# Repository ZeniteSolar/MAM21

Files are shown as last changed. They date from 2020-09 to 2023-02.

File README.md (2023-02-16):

# MAM21
**M**ódulo de **A**cionamento do **M**otor 2021

Embarcação Guarapuvu II

Equipe Zênite Solar

### About
High current >150A Electronic Speed Controller for **[ME0909](https://www.electricmotorsport.com/me0909-pmdc-motor-12-48v-4-hp-cont-12-8-hp-pk.html)** motor, with CANBus.

### Images

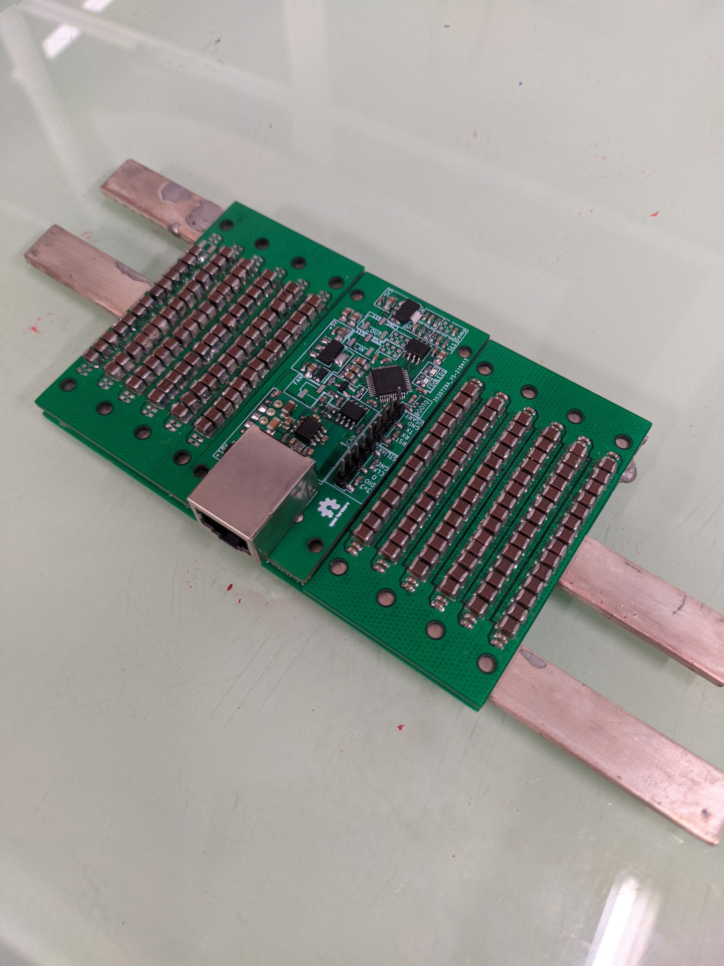
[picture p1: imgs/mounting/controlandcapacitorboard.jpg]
board

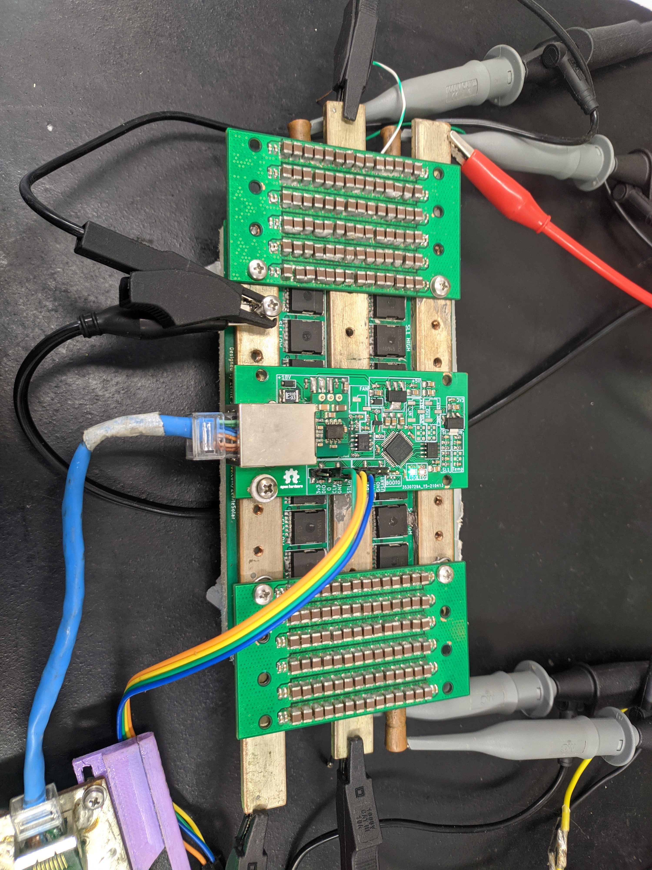
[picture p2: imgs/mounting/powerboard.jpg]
board

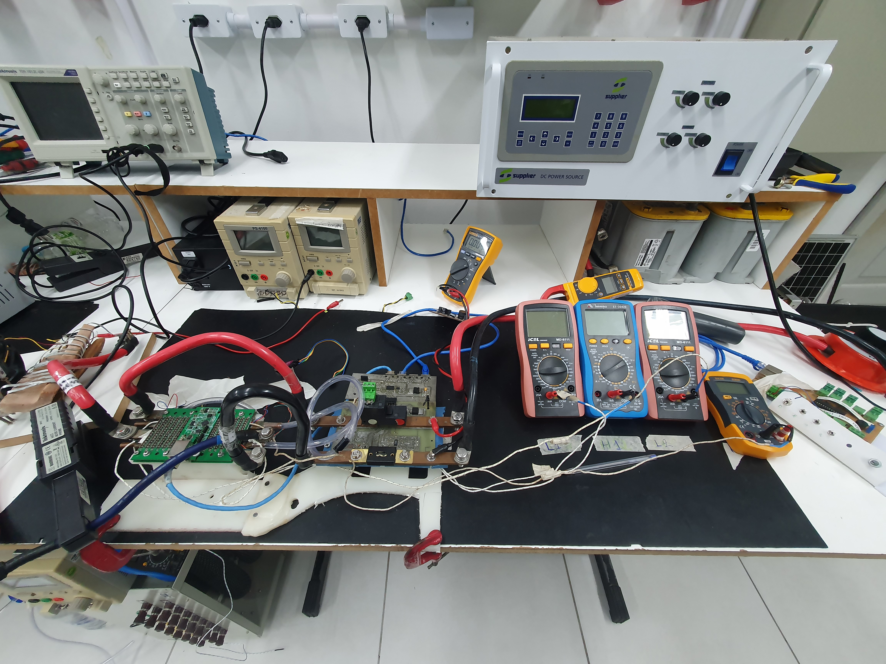
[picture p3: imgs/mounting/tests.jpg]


### Sobre
Este módulo é responsável por realizar o acionamento de um motor de imã permanente, controlando sua velocidade e sentido de rotação.



### Requisitos de projeto

1. **Acionamento do motor**
   - Permitir o acionamento nos dois sentidos de rotação
   - Permitir o controle em malha fechada
     - Corrente/Torque
     - Tensão/RPM

2. **Proteções**
   - Sobre-temperatura do motor
   - Sobre-temperatura do acionamento
   - Sobre-tensão de entrada
   - Sobre-corrente de saída
   - Falha de comunicação
   - Desconexão dos mosfets de potência
     - Garantir que os mosfets permaneçam desligados se a placa de controle for removida
   - Lógica para início de funcionamento
     - O motor só pode ser acionado se o procedimento de início for seguido na sequência correta
       - Dead man`s switch conectado
       - Sistema elétrico ativado
       - Potenciômetro em zero
       - Chave do motor ligada

3. **Interfaces**
   - Ser controlado pela rede CANBUS implementada na embarcação
   - Sinalização por meio de LEDs
   - Permitir debug pela serial

### Abordagens

Especificações do conversor

| Tensão de Entrada | 20 ~ 60 V |
| ---: | :--- |
| Tensão de Saída | 0 ~ 48V |
| Corrente de Saída | 150 A |
| Eficiência | > 80% |

Dados os requisitos e especificações apresentadas anteriormente, foi definido que a topologia utilizada será um conversor ***chopper***, por não haver necessidade de elevação de tensão e por este permitir a variação da tensão média na carga mantendo uma boa eficiência. 

Em um motor DC, a inversão de seu sentido de rotação é feita com a inversão da polaridade, obtida conforme a lógica de acionamento das chaves da ponte H. Uma característica da ponte H completa é que além da inversão de polaridade é possível criar lógicas de acionamento para frear o motor. Importante lembrar que **AS CHAVES DO MESMO BRAÇO NUNCA DEVEM SER ACIONADAS AO MESMO TEMPO**, sob pena de destruição das chaves ou danos ao sistema elétrico da embarcação.

Para que seja possível o monitoramento dos parâmetros do motor e para fechar a malha de controle, precisarão ser empregados sensores para o monitoramento da corrente e rotação do motor. O diagrama abaixo apresenta a topologia utilizada para o acionamento.



O motor utilizado pela embarcação é o **[ME0909](https://www.electricmotorsport.com/me0909-pmdc-motor-12-48v-4-hp-cont-12-8-hp-pk.html)**. Este motor possui tensão de operação de 12 ~ 48V e 4,8 kW de potência nominal.

A rede CAN utilizada será a já implementada atualmente.

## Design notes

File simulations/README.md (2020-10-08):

# Embedded System Simulation with PSIM

O objetivo deste documento é registrar a implementação inicial de uma simulação
de sinais mistos (mixed signals simulation) de um chopper operando nos quatro
quadrantes, usando o PSIM.

## Table Of Contents

- [1.0. Chopper](#10-chopper)
- [2.0. Pilot Controller](#20-pilot-controller)
- [3.0. Signal Conditioning](#30-signal-conditioning)
- [4.0. PWM Peripheral](#40-pwm-peripheral) 
- [5.0. Embedded Controller](#50-embedded-controller)
  - [5.1. ADC Inputs](#51-adc-inputs)
    - [5.1.1. ADC Test](#511-adc-test)
  - [5.2. Digiital Inputs](#52-digital-inputs)
  - [5.3. Outputs](#53-outputs)
    - [5.3.1. PWM](#531-pwm)
- [6.0. Firmware](#60-Firmware)
- [7.0. Test](#70-Test)  

---

## 1.0. Chopper

O circuito do chopper foi implementado de modo a possibilitar o comando
individual das chaves, assim como a medição das correntes e tensões de entrada e
saída, além de separar a entrada e saída, a fim de facilitar mudanças na
simulação.

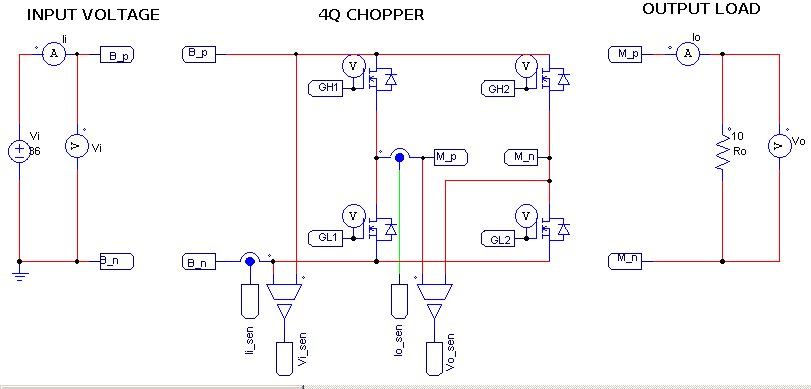
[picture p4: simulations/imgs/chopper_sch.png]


---

## 2.0. Pilot Controller

O Pilot Controller aqui é utilizado para simular comandos supostamente
utilizados pelo piloto, como:

- ligar/desligar o acionamento (Enable)
- ligar/desligar a reversão do sentido de rotação (Rev)
- ligar/desligar a regeneração (Regen)
- modificar a potência % desejada (Power)

O esquemático utilizado e os sinais gerados podem ser vistos nas figuras abaixo:

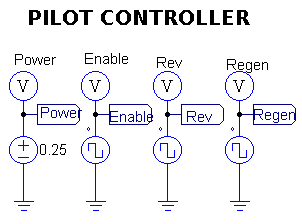
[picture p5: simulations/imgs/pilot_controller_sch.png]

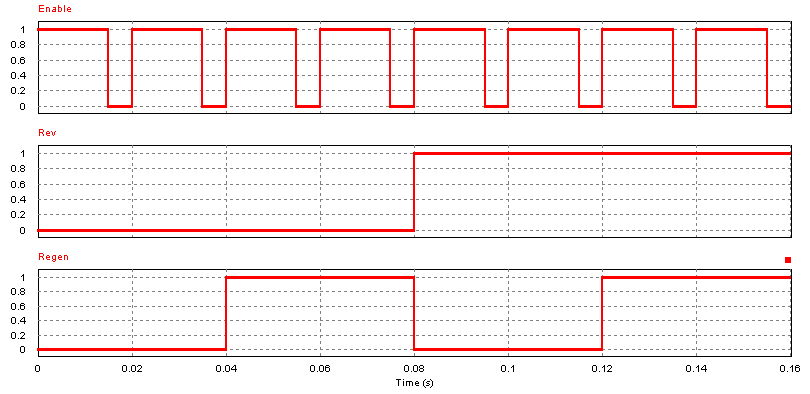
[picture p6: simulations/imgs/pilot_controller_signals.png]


---

## 3.0. Signal Conditioning

O condicionamento dos sinais aqui é feito com um filtro passa-baixa, ganho e
offset (quando é necessário medir sinais positivos e negativos - full-range).

- O filtro passa-baixa é primeira ordem com a frequência de corte em 100Hz e
  pode ser facilmente alterada.
- O ganho aplicado é a razão entre a tensão máxima do ADC e o valor máximo a ser
  medido. No caso do full-range, é utilizada a metade da tensão máxima do ADC.
- Quando full-range, é aplicado um offset também com a metade da tensão máxima
  do ADC, afim de garantir o máximo aproveitamento de sua escala.

O esquemático utilizado e os sinais gerados podem ser vistos nas figuras abaixo:

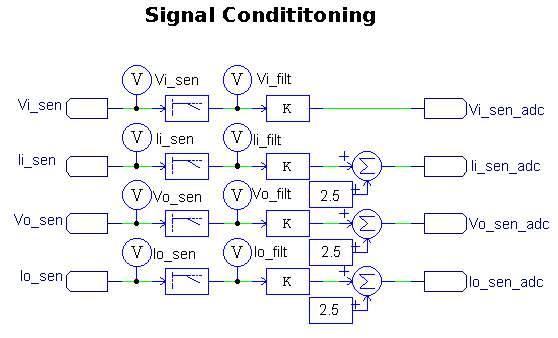
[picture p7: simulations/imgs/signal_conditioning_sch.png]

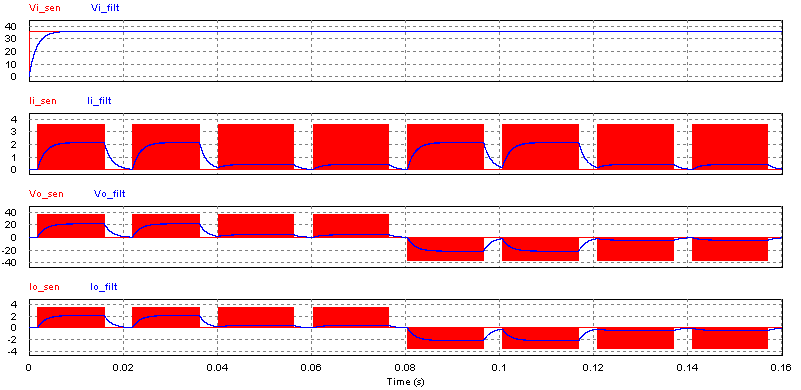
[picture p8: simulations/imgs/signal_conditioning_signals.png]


---

## 4.0. PWM Peripheral

O periférico de PWM é realizado com a comparação entre um sinal dente de serra
e uma referência que define o tempo ligado (que percentualmente é o duty-cycle).
O sinal resultante é um PWM com frequência igual à frequência do sinal dente de
serra utilizado (Freq), e com duty-cycle proporcional ao sinal DT.

Para acionar os braços da ponte H, são gerados dois sinais PWM controlados
individualmente, juntamente com seus sinais complementares. Os sinais
não complementares acionam as chaves de cima, enquantos os sinais complementares
acionam as chaves de baixo.

Por ser uma simulação idealista, não foi implementado o recurso de tempo-morto
(deadtime), mas se os mosfets não fossem ideias, este recurso seria
indispensável para impedir que o curto de braço ocorresse a cada período de
chaveamento.

O esquemático utilizado e os sinais gerados podem ser vistos nas figuras abaixo:

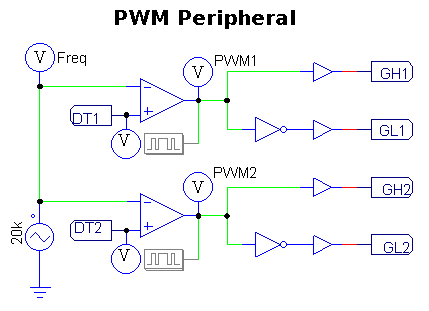
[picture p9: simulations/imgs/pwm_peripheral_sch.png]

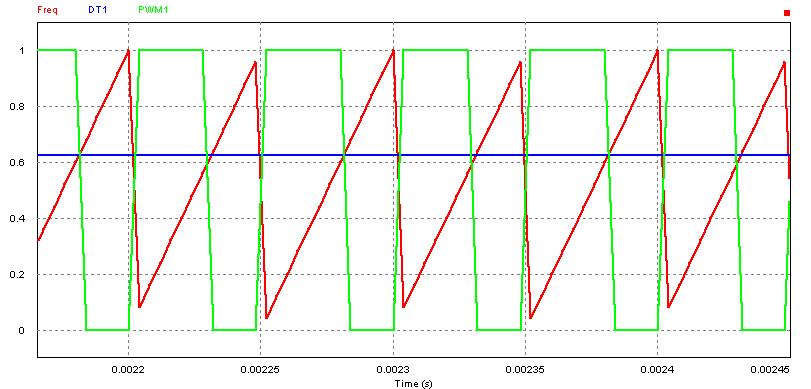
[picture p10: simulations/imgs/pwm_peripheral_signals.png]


---

## 5.0. Embedded Controller

O controlador embarcado é implemetado utilizando um elemento C Block, possuindo
inicialmente 8 entradas e 20 saídas, que podem ser expandidas e que permitem a
interação do código escrito em C com as variáveis presentes na simulação.

### 5.1. ADC Inputs

Para implementar o ADC como um periférico do tipo SAR com *N* canais
compartilhando um único comparador, poderia ser utilizado uma sequência de
blocos como o 'Quantization function block', e 'Sampling/hold block', mas para
ter um melhor domínio da solução (e também para deixá-la mais portável para
algum outro simulador), foi optado realizar todas estas funções em um bloco
'C Block', implementando a quantização, o segurador, e também o atraso entre
a amostragem dos canais multiplexados.

O sinal para acionamento da amostragem de cada canal é controlado por um sinal
de clock `ADC_CLOCK`, gerado pelo bloco CONTROLLER. Sempre que uma conversão é
finalizada, o bloco SAR_ADC gera um pulso em uma de suas saídas, chamado 
`END_OF_CONVERSION`, que por sua vez é lido pelo bloco CONTROLLER e atua como
o sinal de interrupção do microcontrolador, chamando a função `adc_interrupt()`,
que faz a conversão e guarda os valores em variáveis globais do CONTROLLER.

O código escrito em C está contido no arquivo [chopper_4q__sar_adc.c](chopper_4q__sar_adc.c).

#### 5.1.1. ADC Test

Por se tratar de uma implementação que precisa ser testada individualmente, uma
segunda simulação foi criada, contendo o mínimo necessário para testar a
implementação. O teste faz sucessivas conversões com os 4 canais, amostrando o
mesmo sinal, que deve ser comparado com o sinal original (chamado de `in`).

O esquemático utilizado e os sinais gerados podem ser vistos nas figuras abaixo:

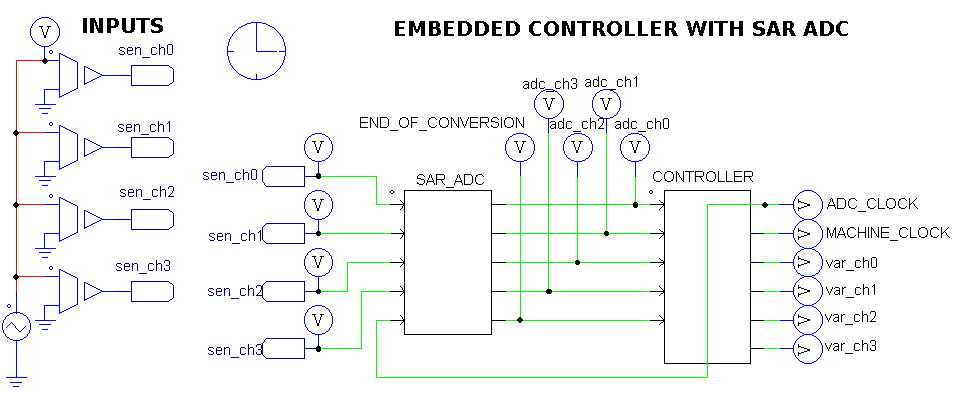
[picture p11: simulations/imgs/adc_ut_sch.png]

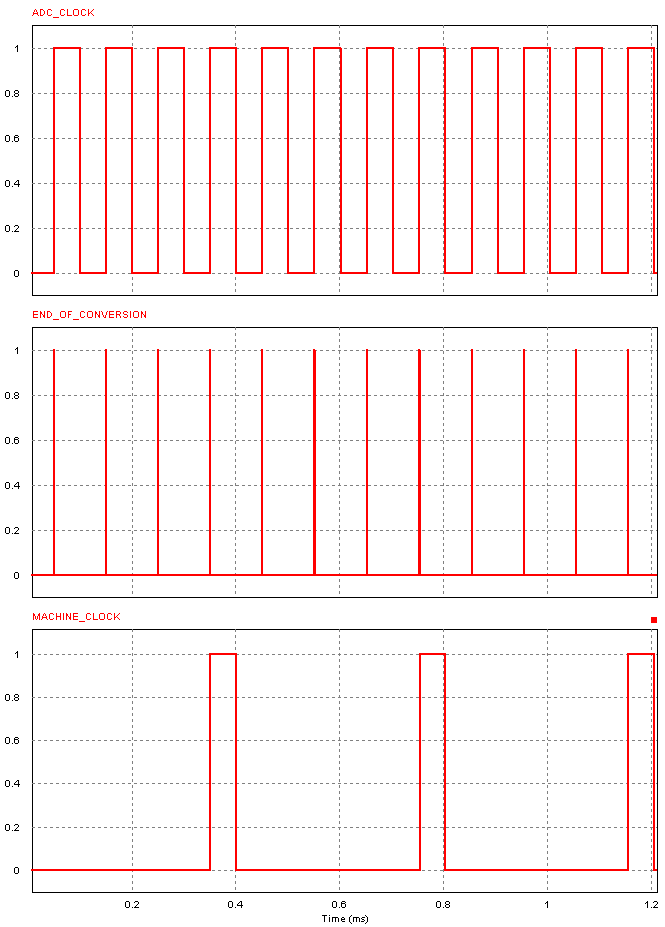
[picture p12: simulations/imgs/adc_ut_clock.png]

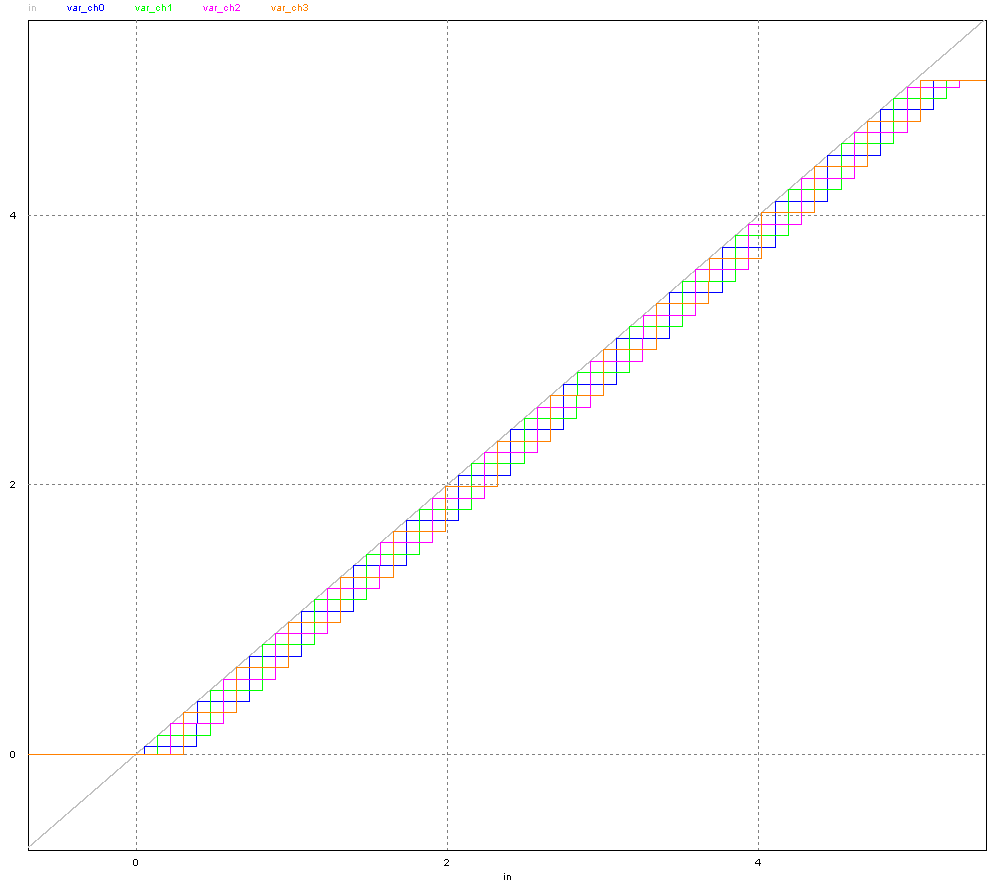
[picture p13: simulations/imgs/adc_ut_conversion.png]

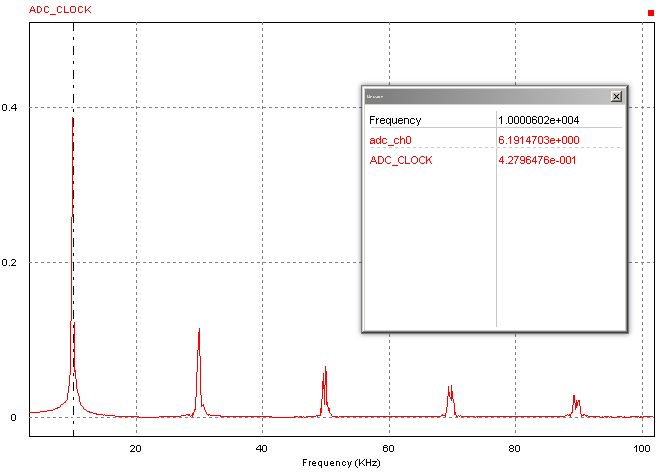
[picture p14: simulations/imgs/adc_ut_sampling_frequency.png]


A figura abaixo detalha o sinal original e o sinial lido pelo CONTROLLER:

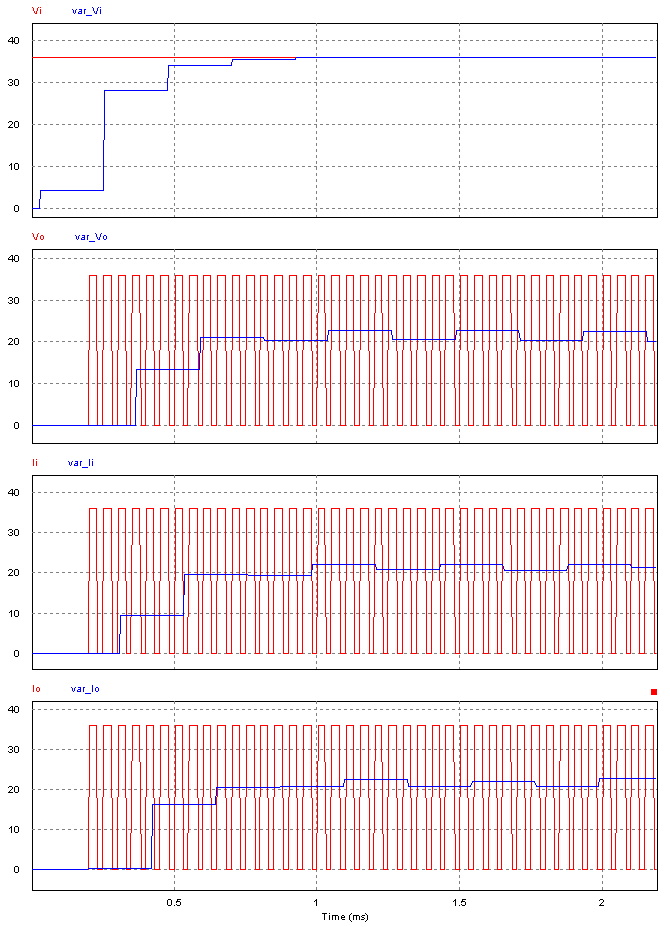
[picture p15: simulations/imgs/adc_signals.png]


### 5.2. Digital Inputs

Os sinais digitais são diretamente conectados no CONTROLLER, e seu threshold é
definido dentro do código (0.5) usando um operador ternário para transformar
no valor `0` ou `1`.

### 5.3. Outputs

Os sinais relevantes do CONTROLLER são externalizados utilizando diversas portas
de saída monitorados por multímetros.

#### 5.3.1. PWM

O valor de duty-cycle computado pelo controlador é externalizado passando por um
quantizador, de modo a transformar o valor interno em um sinal quantizado com a
precisão em bits que um timer utilizado no periférico permitir. Inicialmente foi
utilizado 7 bits.

---

### 6.0. Firmware

No C Block, é possível escrever código em 4 abas. Aqui usamos apenas duas delas:

- `FUNCTIONT TYPE (Variable/Function definitions)` é onde definimos as variáveis
  e funções, que seria análogo aos arquivos incluídos por `#include`, sendo
  headers ou sources.
- `RunSimUser Fcn` é a função que a simulação chama a cada iteração de intervalo
  timestep da simulação.

O código inicial pode ser visto no arquivo [chopper_4q__embedded_controller.c](chopper_4q__embedded_controller.c).

Todos os testes realizados neste documento utilizram ele, sem nenhuma
modificação drástica entre as etapas, a fim de documentar um estado básico e 
sólido para as possíveis centenas de iterações com a simulação até o
desenvolvimento final do sistema.

---

## 7.0. Test

Com todas as partes integradas na mesma simulação, podemos simular a interação
entre um sistema físico e seu firmware.

Na figura abaixo pode ser visto os sinais de corrente e tensão acionando uma 
carga resistiva nos quatro quadrantes em decorrência dos controles do piloto.

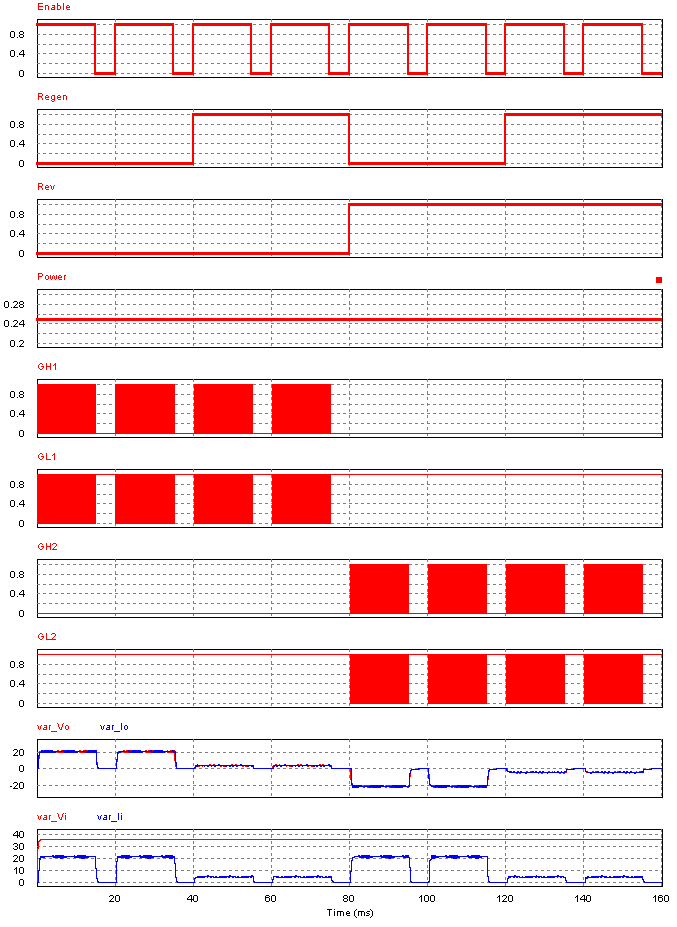
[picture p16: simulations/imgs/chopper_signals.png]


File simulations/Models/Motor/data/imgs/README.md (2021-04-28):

# Teardown of Motenergy ME0909 PMDC Motor











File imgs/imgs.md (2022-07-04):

# Modulation.png
C1 = VgsCH1_H
C2 = VgsCH1_L
C3 = VgsCH2_H
C4 = VgsCH2_L
motor.png C1 = motor modulation

# Vds_with_cap.png and Vds_without_cap.png
difference between use asymmetrical capacitor bank and symmetrical

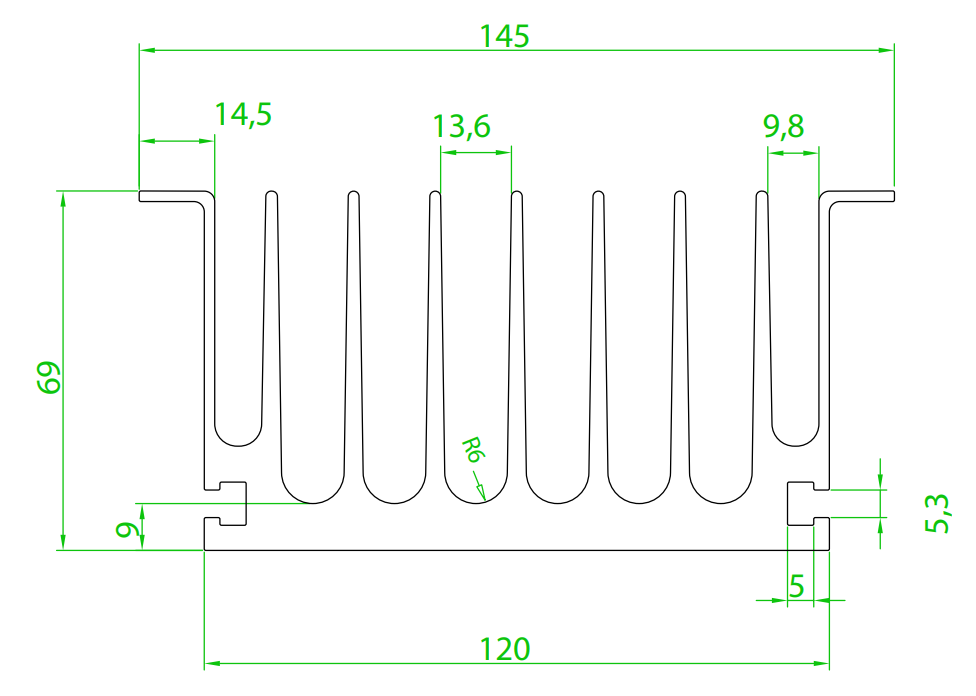
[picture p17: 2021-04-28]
hardware/Mechanical/heatsink.png

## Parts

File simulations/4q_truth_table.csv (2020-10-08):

quadrante | "Rev" | "Break" | "1H" | "1L" | "2H" | "2L"
Q1 | 0 | 0 | "DT" | "!DT" | 0 | 1
Q2 | 0 | 1 | "!DT" | "DT" | 0 | 1
Q3 | 1 | 0 | 0 | 1 | "DT" | "!DT"
Q4 | 1 | 1 | 0 | 1 | "!DT" | "DT"

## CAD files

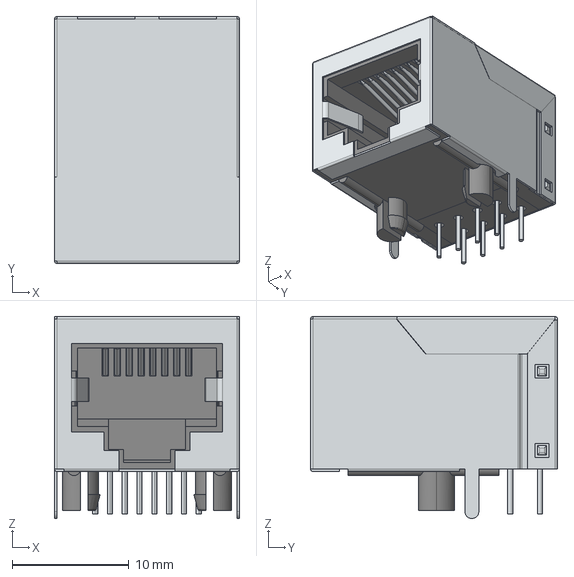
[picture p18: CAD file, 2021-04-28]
hardware/Controle/Bibliotecas/rj45.step
15.9 x 21.2 x 17.3 mm

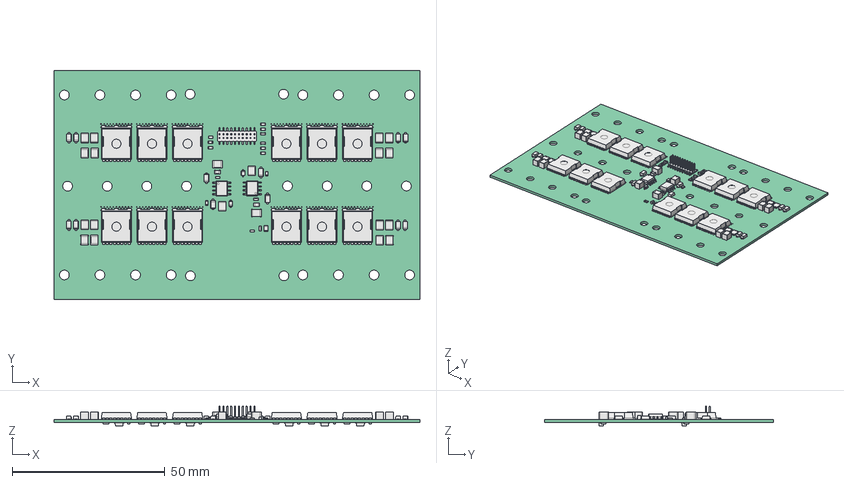
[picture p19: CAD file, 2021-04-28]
hardware/Mechanical/switches.FCStd
120.0 x 75.0 x 6.50 mm
Rsn108_R_1210_3225Metric_607492AA x 32
R117_R_0603_1608Metric_606C02F8 x 84
C134_C_0603_1608Metric_606C0308 x 24
Dsn108_D_SOD_123F_6074702B x 96
U102_SOIC_8_1EP_39x49mm_P127mm_606CF202 x 8
Q112_Infineon_PG_HSOF_8_1_606C635D x 48
Csn108_C_1210_3225Metric_60746C07 x 48
TH101_R_0805_2012Metric_606C0318 x 52
C111_C_0805_2012Metric_606CF1B7 x 8
D118_D_SOD_323_606ADB94 x 8
J105_PinHeader_2x10_P127mm_Vertical_SMD_606D32DE x 4
Pcb_57a1 x 3

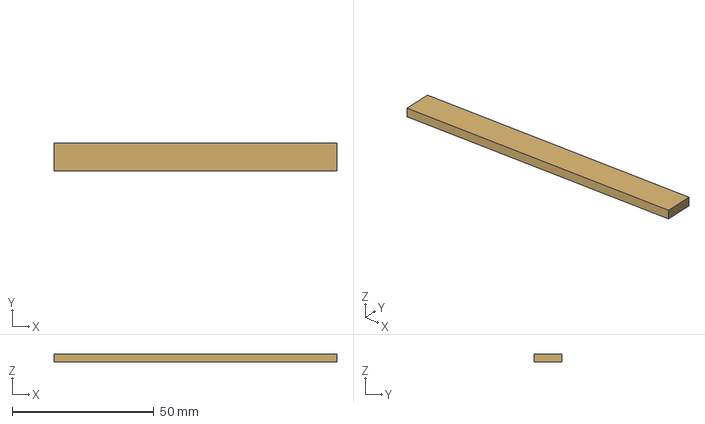
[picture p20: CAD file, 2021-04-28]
hardware/Switches/3D/busbar.step
100.0 x 10.0 x 3.00 mm

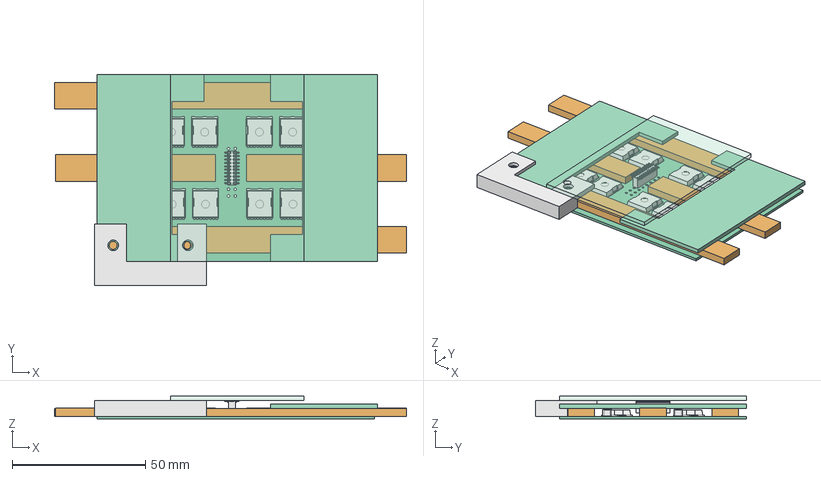
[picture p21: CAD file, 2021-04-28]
hardware/Switches/Swiches.FCStd
131.9 x 79.0 x 8.60 mm
Pcb_57a1
R110_R_1210_3225Metric_605E0A44 x 4
C106_C_1210_3225Metric_605E02F8 x 4
Q112_Infineon_PG_HSOF_8_1_605C81D9 x 12
PinSocket_2x10_P127mm_Vertical_SMD001
PinHeader_2x10_P127mm_Vertical_SMD001

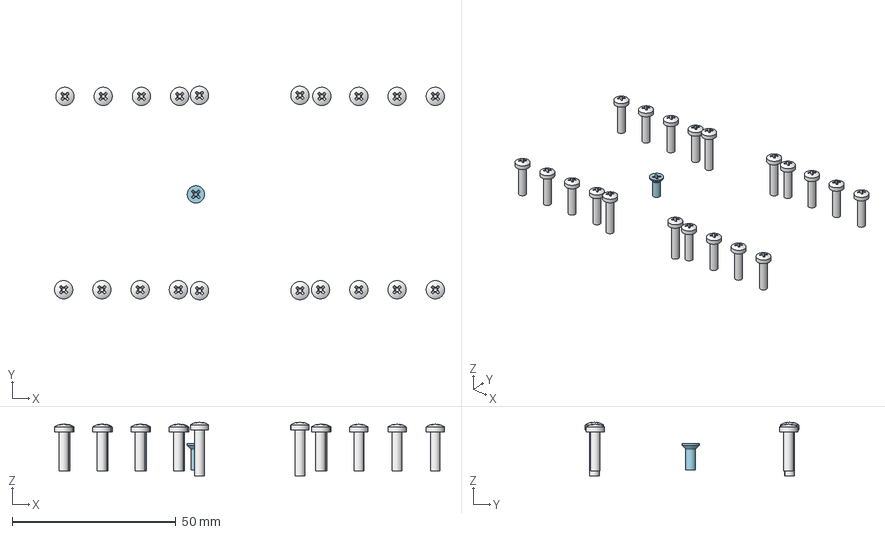
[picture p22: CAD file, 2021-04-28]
hardware/Mechanical/ESC.FCStd
119.0 x 65.2 x 16.3 mm
M3x12-Screw x 2
M3x12-Screw1523 x 2
M3x12-Screw1524 x 2
M3x12-Screw1533 x 2
M3x12-Screw1525 x 2
M3x12-Screw1526 x 2
M3x12-Screw1527 x 2
M3x12-Screw1528 x 2
M3x12-Screw1529 x 2
M3x12-Screw1534 x 2
M3x12-Screw1530 x 2
M3x12-Screw1535 x 2
M3x12-Screw1536 x 2
M3x12-Screw1537 x 2
M3x12-Screw1531 x 2
M3x12-Screw1532 x 2
M3x14-Screw x 2
M3x14-Screw118 x 2
M3x14-Screw119 x 2
M3x14-Screw120 x 2
M3x8-Screw x 2

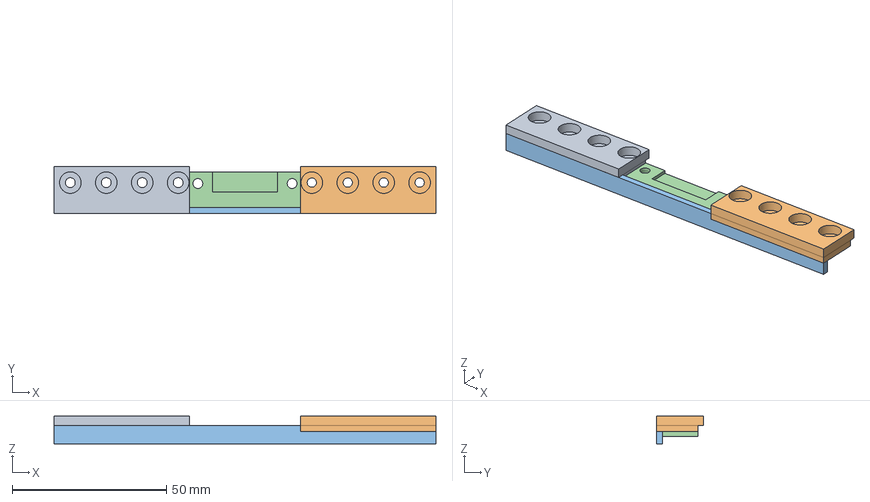
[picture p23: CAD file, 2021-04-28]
hardware/Mechanical/support1.FCStd
124.0 x 15.2 x 9.00 mm

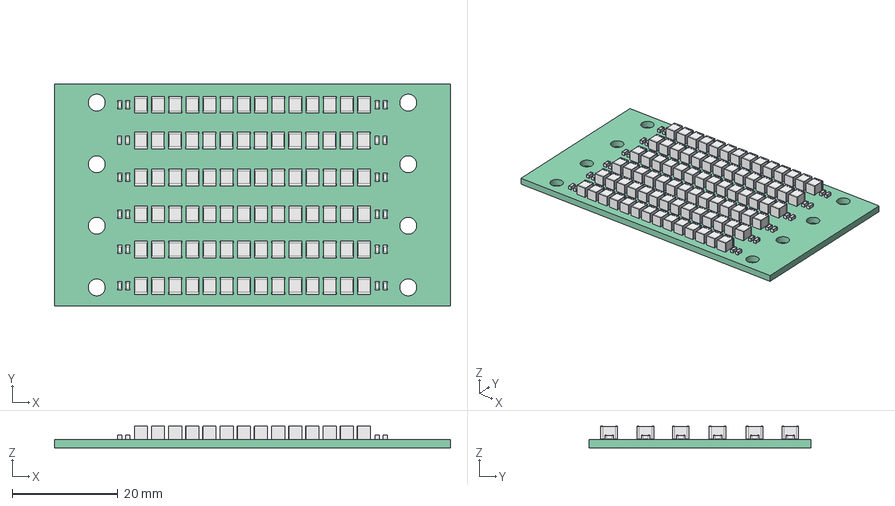
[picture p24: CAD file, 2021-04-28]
hardware/Mechanical/caps.FCStd
75.0 x 42.0 x 4.10 mm
C230_C_1210_3225Metric_6077E91F x 336
C232_C_0603_1608Metric_6077F2BE x 96
Pcb_1fb6 x 3

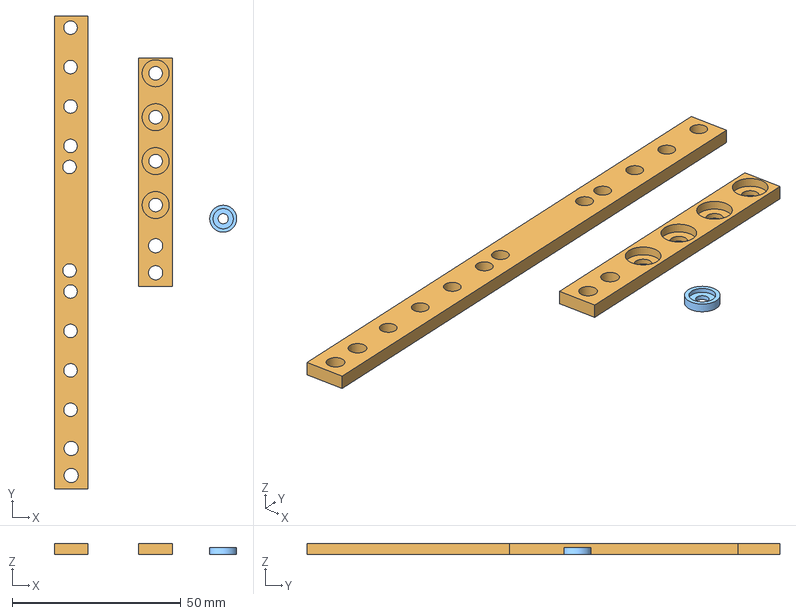
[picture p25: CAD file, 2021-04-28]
hardware/Mechanical/busbars.FCStd
54.0 x 140.0 x 3.20 mm
bar1_Body
bar2_body
insulator

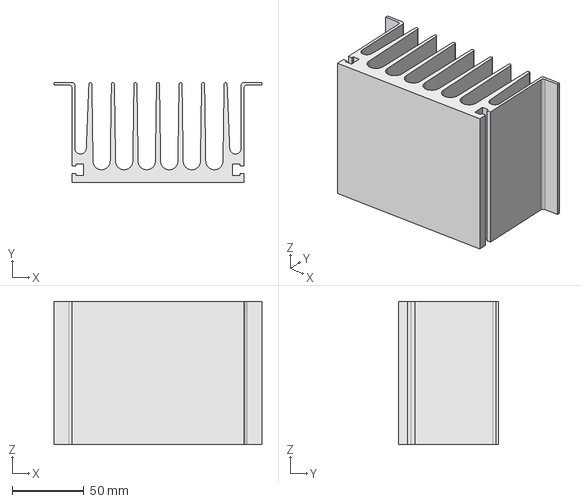
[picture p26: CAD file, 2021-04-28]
hardware/Mechanical/heatsink.FCStd
145.0 x 70.0 x 100.0 mm

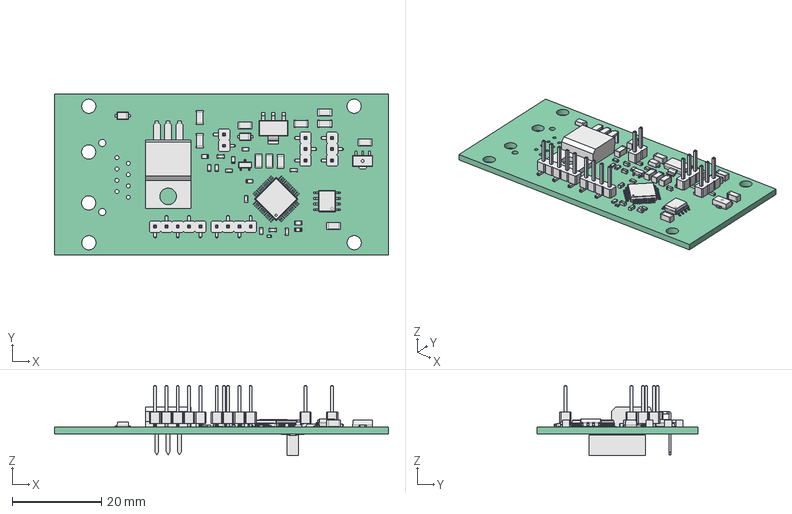
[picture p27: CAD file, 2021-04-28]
hardware/Mechanical/controle.FCStd
75.0 x 36.1 x 15.7 mm
R103_R_0603_1608Metric_607532D5 x 32
Q101_SOT_23_6075318C x 4
C104_C_1206_3216Metric_60753A85 x 44
U401_SOT_89_3_607525BD x 4
J102_PinHeader_1x05_P254mm_Vertical_SMD_Pin1Left_607527F2 x 4
D102_D_SOD_123F_60752671 x 8
D501_LED_0603_1608Metric_6077B07B x 4
U601_SOIC_8_39x49mm_P127mm_6075390B x 4
J103_PinHeader_1x02_P254mm_Vertical_SMD_Pin1Left_60752E1C x 4
U501_LQFP_48_7x7mm_P05mm_607528ED x 4
R504_R_0402_1005Metric_6075253D x 4
J101_PinHeader_1x04_P254mm_Vertical_SMD_Pin1Left_60752A18 x 4
C201_C_0603_1608Metric_6075323F x 24
U403_TO-220-3_Horizontal_TabDown_607524A3 x 4
U402_SOT_223_6075262C x 4
J106_PinHeader_1x03_P254mm_Vertical_SMD_Pin1Left_607539D0 x 8
J107_PinSocket_2x10_P127mm_Vertical_SMD_606F5D48 x 4
Pcb_266e x 3

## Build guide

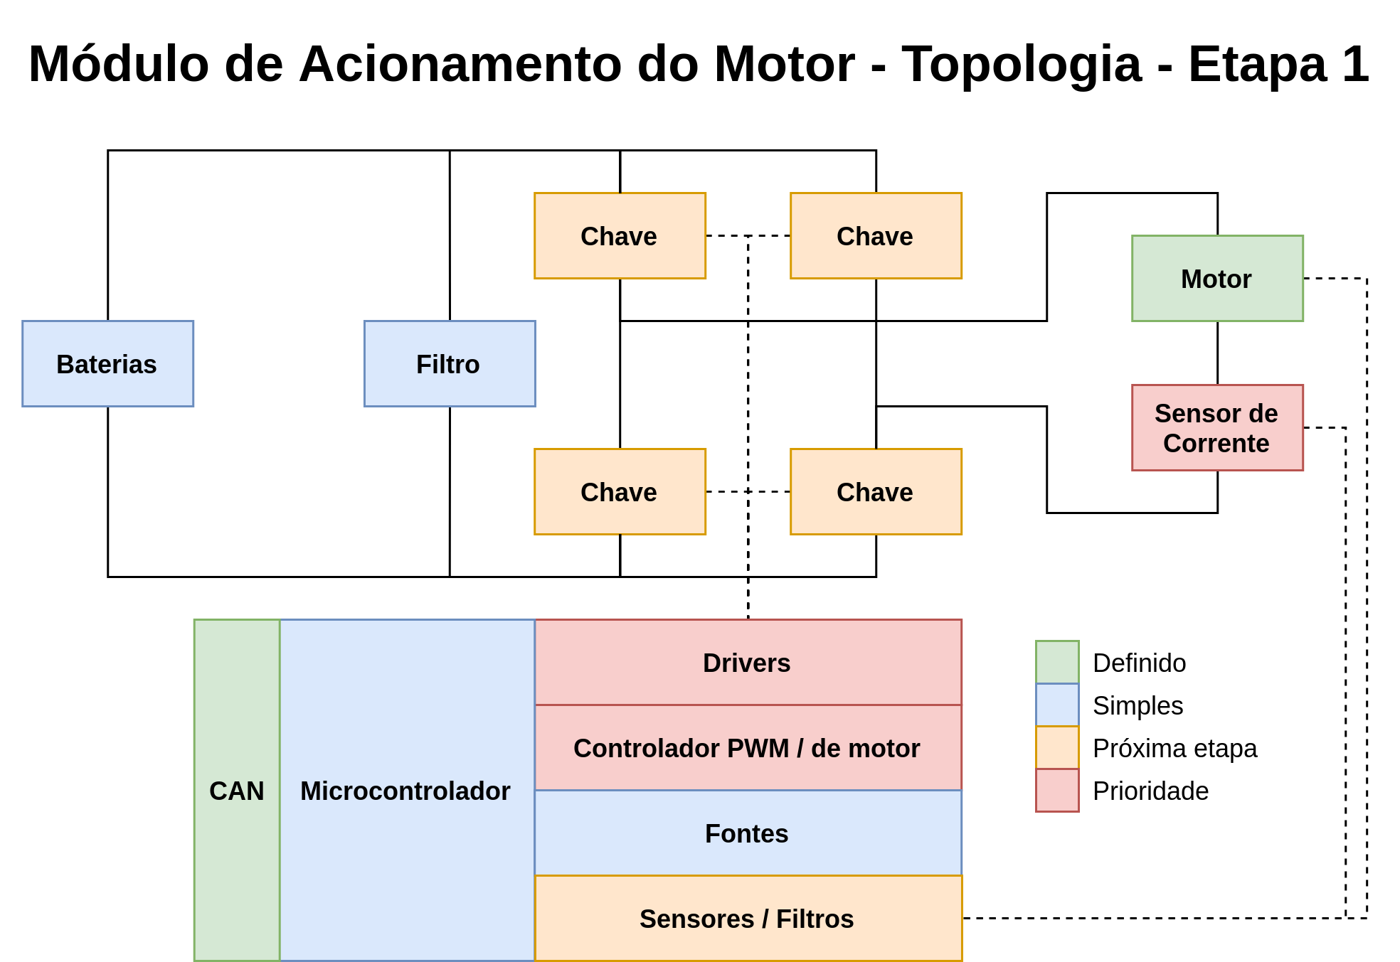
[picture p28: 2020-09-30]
diagrams/topology_step1.png

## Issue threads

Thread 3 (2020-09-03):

Escolher Topologia

joaoantoniocardoso, 2020-09-03:
Pesquisar opções viáveis para topologias, listar as características e localizar referências (app notes, design references, datasheets, projetos opensource, etc).

Closed 2020-09-30.

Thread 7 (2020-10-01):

Definir controlador PWM

joaoantoniocardoso, 2020-10-01:

joaoantoniocardoso, 2022-01-01:
PWM signals are generated by the chosen MCU: [STM32F303CBT6](https://www.mouser.com/ProductDetail/STMicroelectronics/STM32F303CBT6)

Closed 2022-01-01.

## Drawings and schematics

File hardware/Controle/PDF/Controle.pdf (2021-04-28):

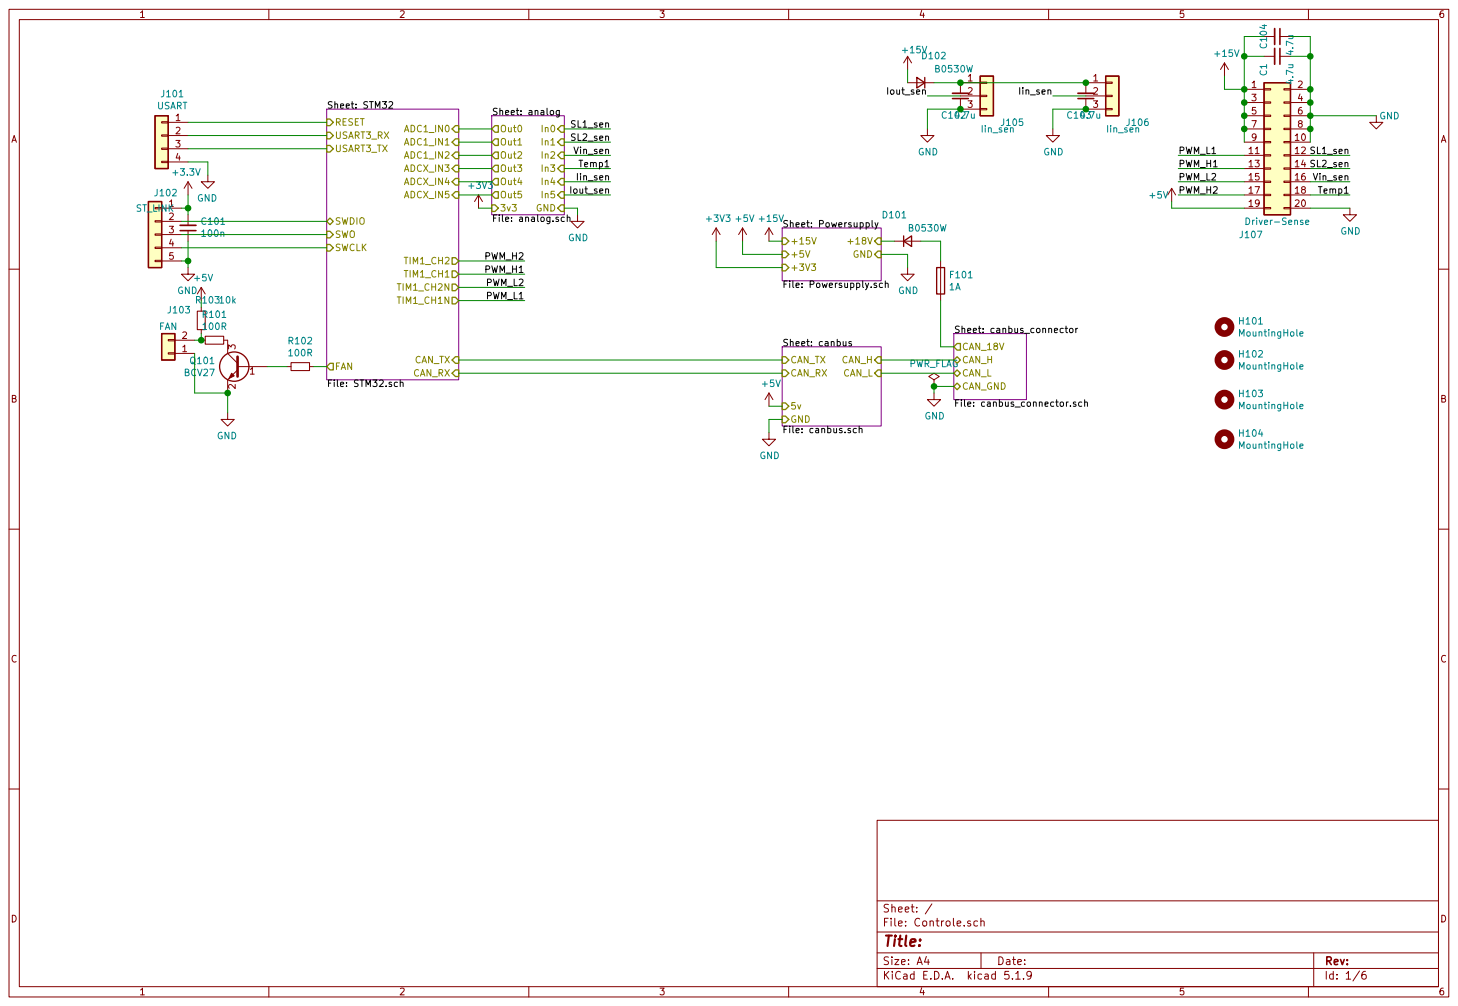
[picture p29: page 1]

Sheet: canbus File: canbus.schCAN_H
CAN_L CAN_TX CAN_RX

Id: 1/6 Title: File: Controle.sch Sheet: /

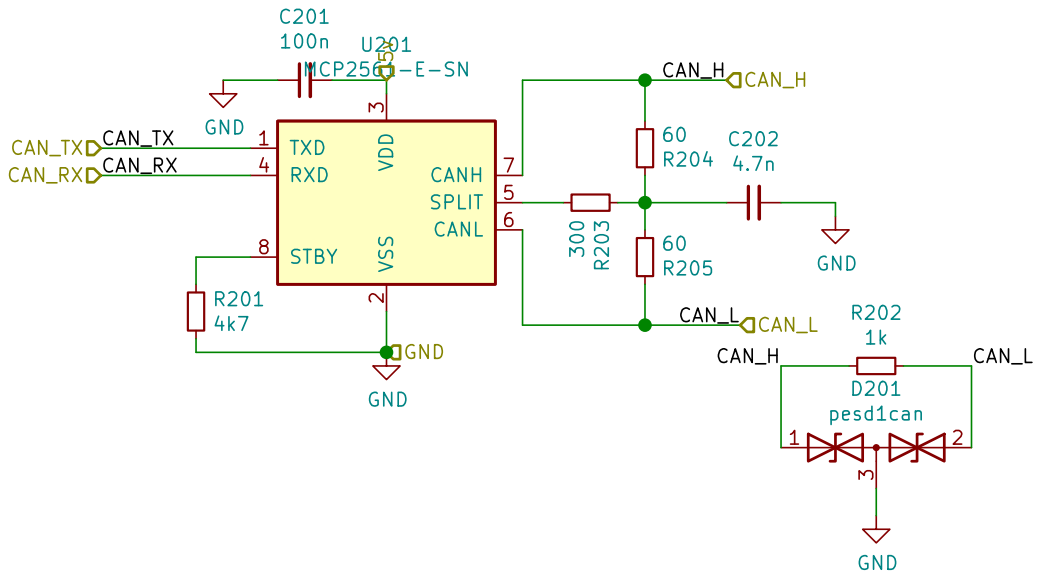
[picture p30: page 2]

3 RXD 4 SPLIT 5 CANL 6 CANH 7 STBY 8 U201 MCP2561-E-SN

Id: 2/6 Title: File: canbus.sch Sheet: /canbus/

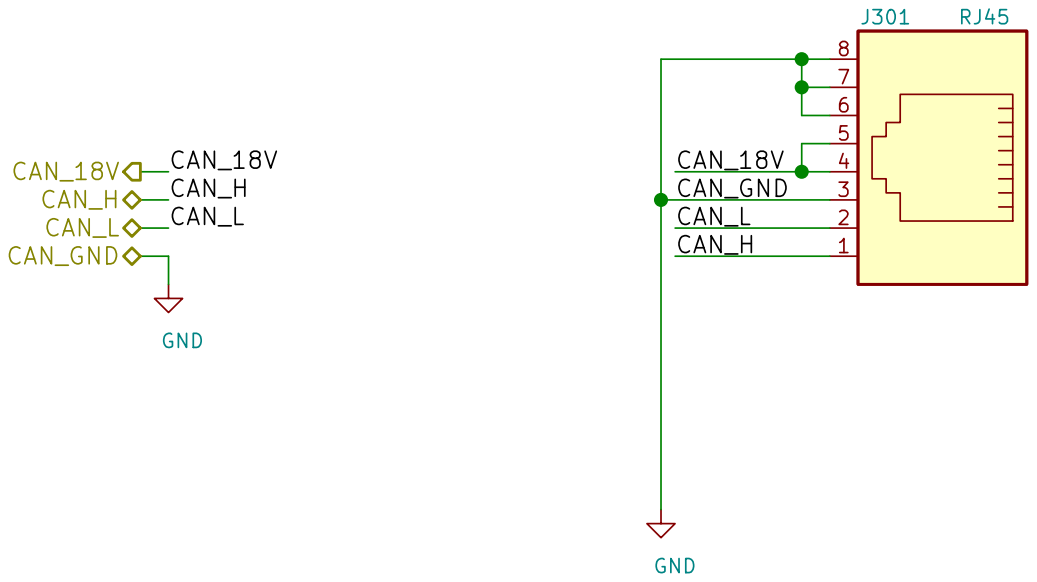
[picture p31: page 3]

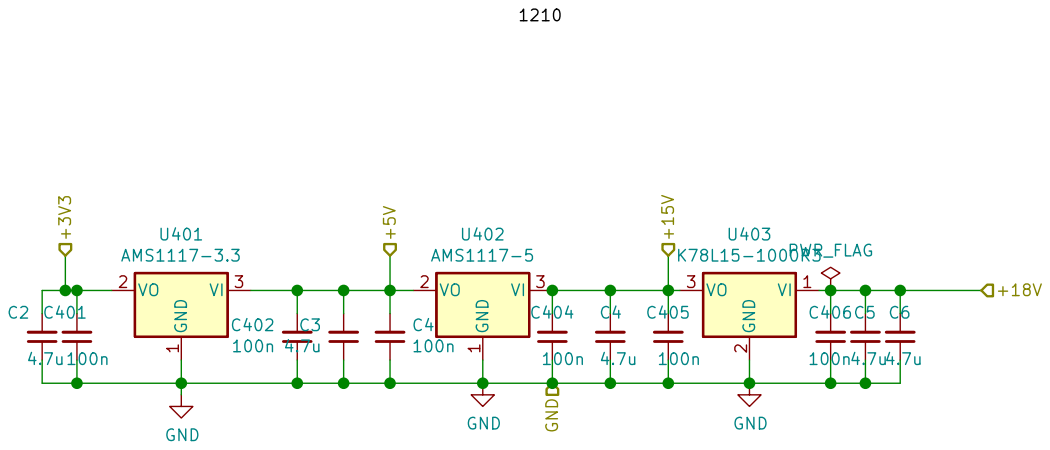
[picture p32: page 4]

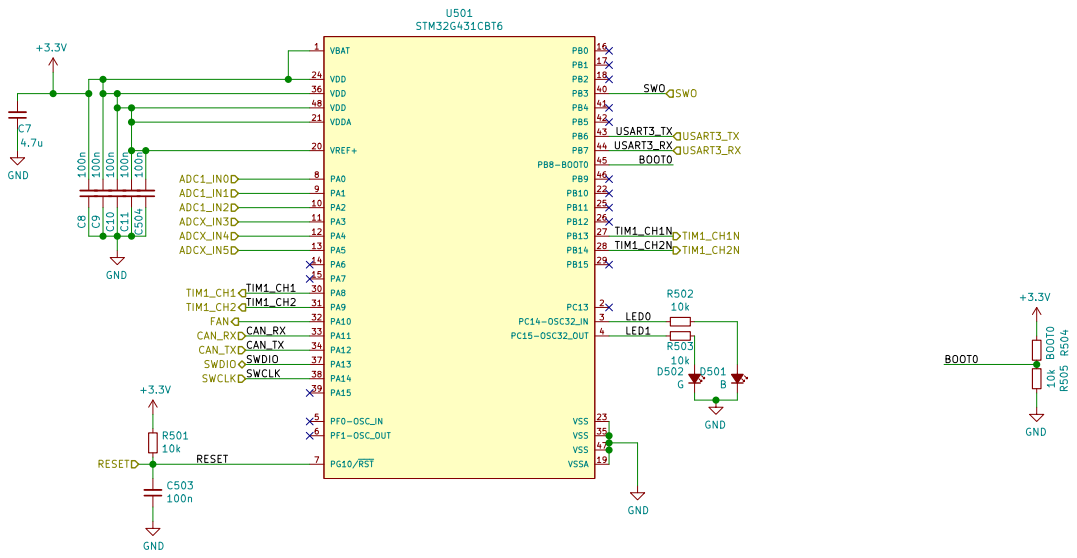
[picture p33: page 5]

Id: 5/6 Title: File: STM32.sch Sheet: /STM32/ GND

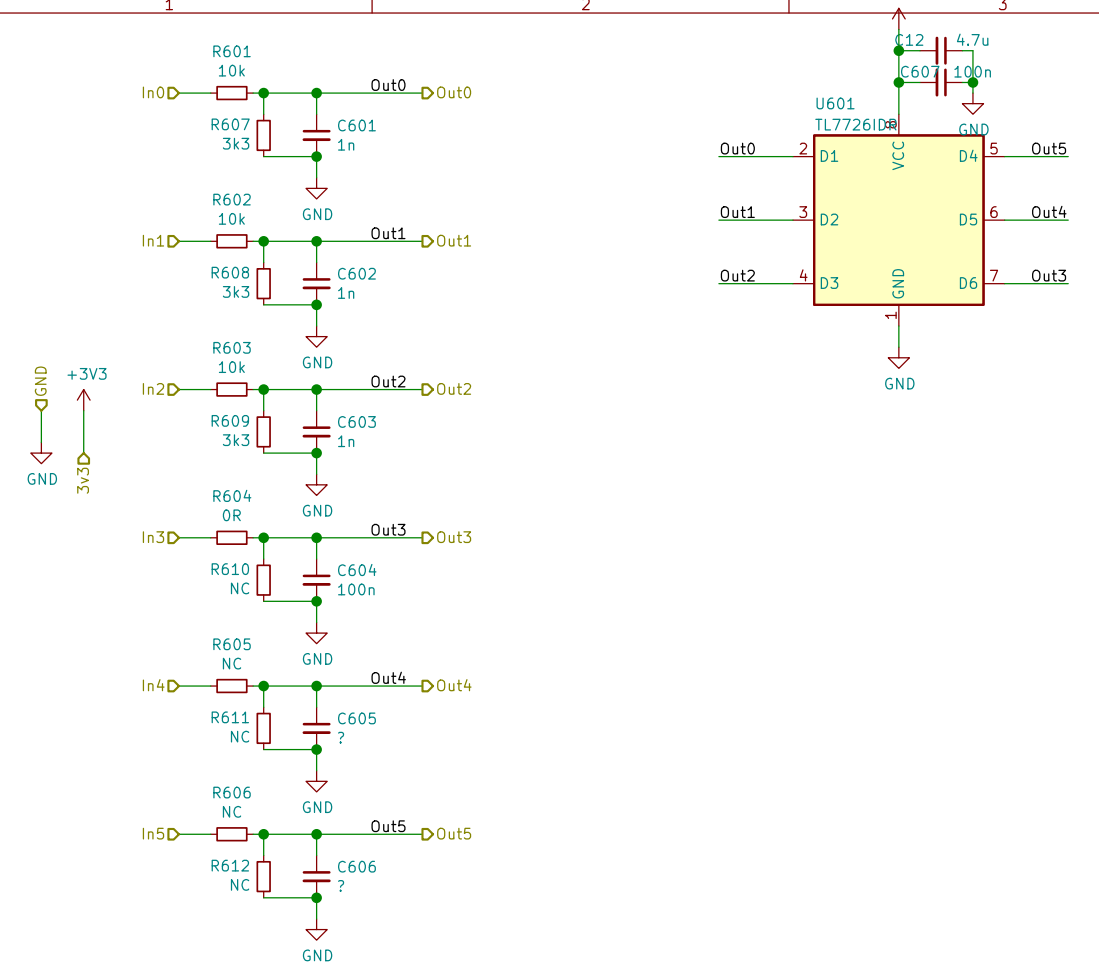
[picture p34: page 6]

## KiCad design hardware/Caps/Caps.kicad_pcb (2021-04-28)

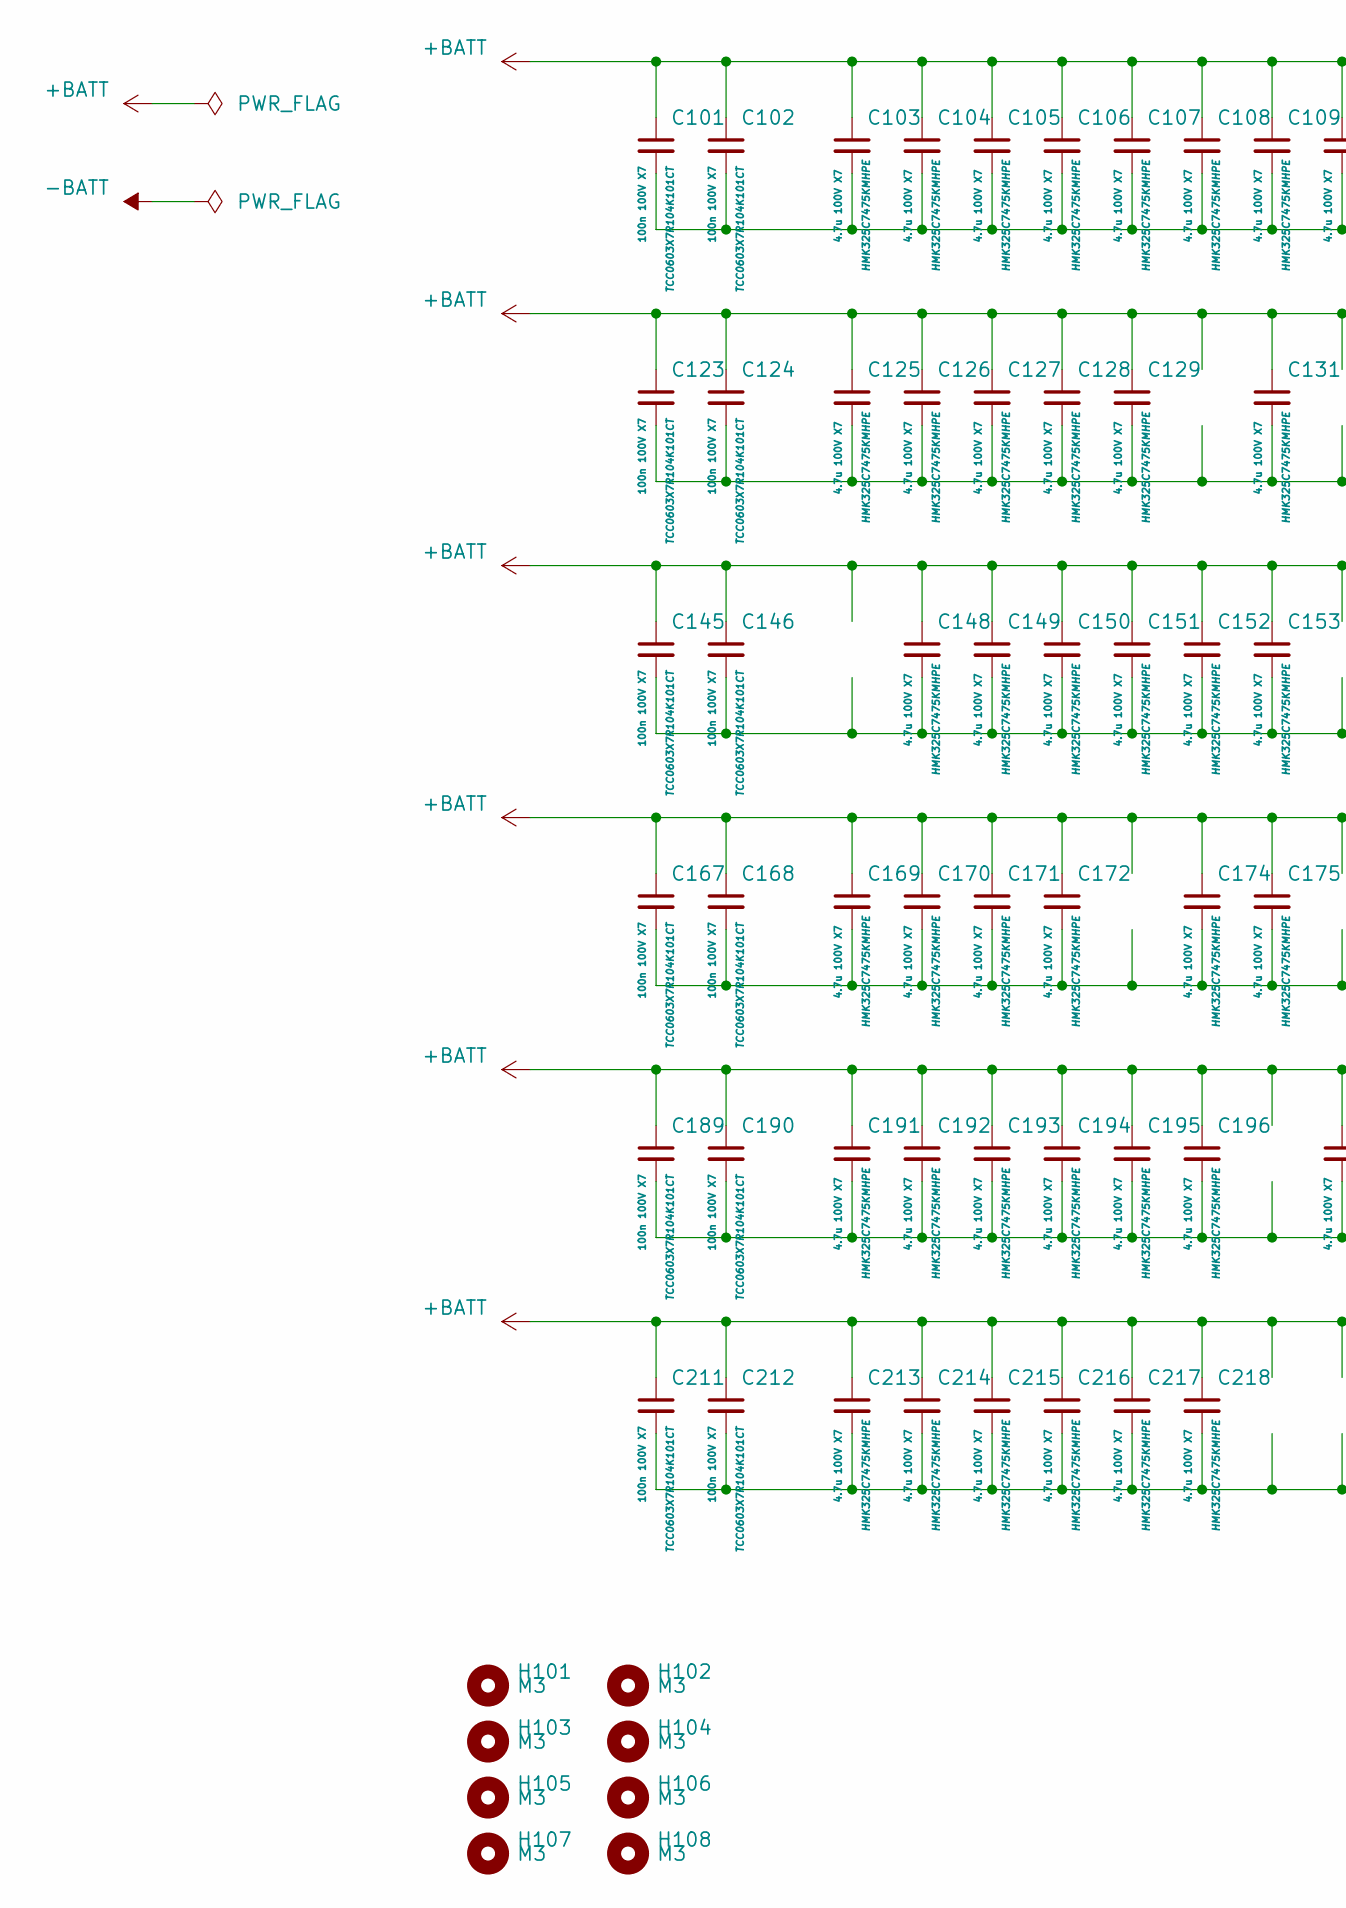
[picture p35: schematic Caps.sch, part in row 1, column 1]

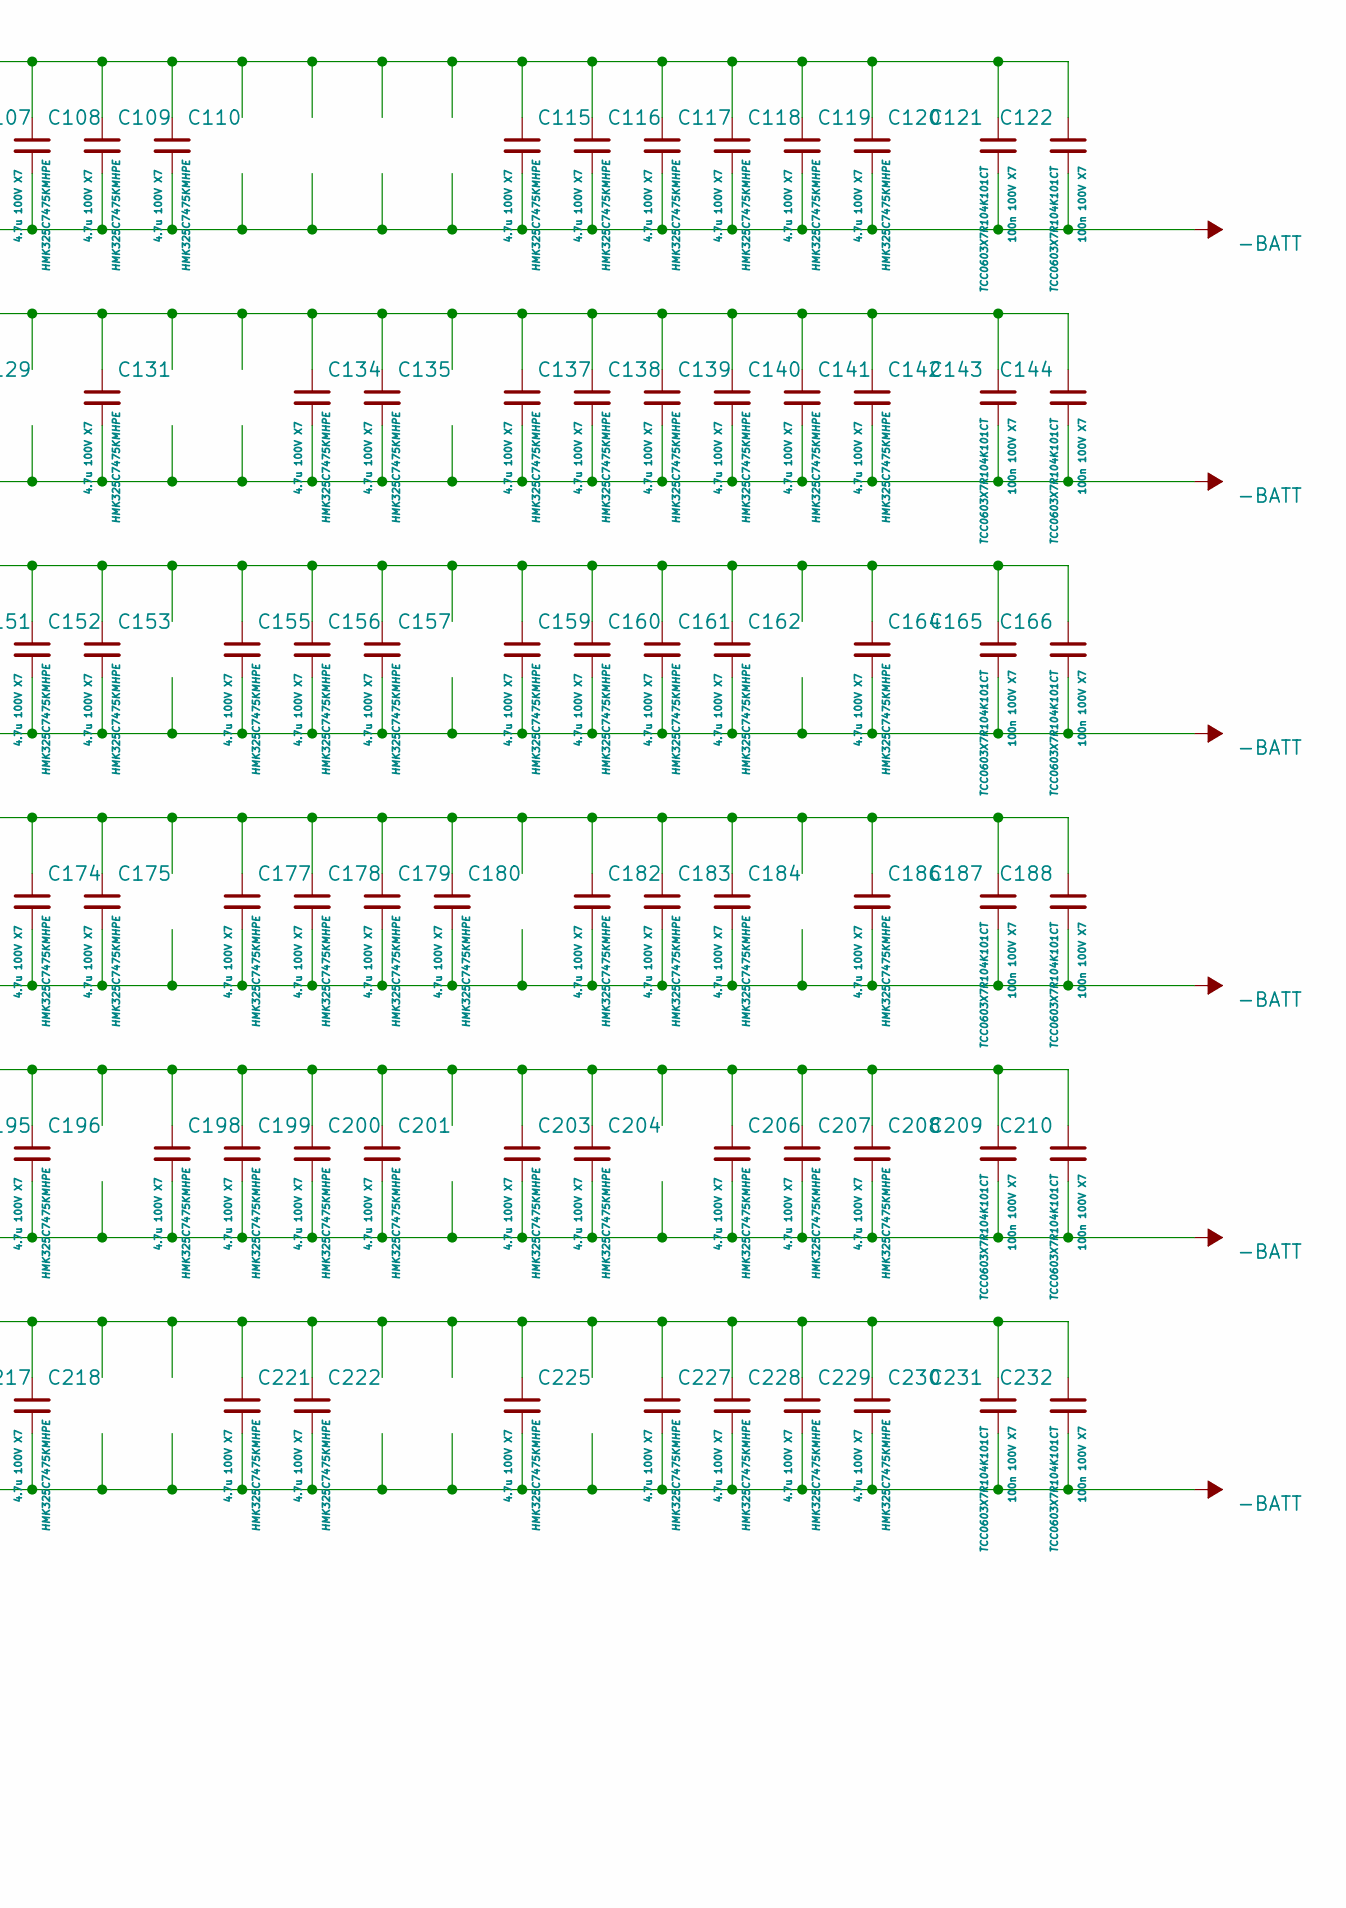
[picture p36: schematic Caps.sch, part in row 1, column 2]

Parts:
C101, C102, C121, C122, C123, C124, C143, C144, C145, C146, C165, C166, C167, C168, C187, C188, C189, C190, C209, C210, C211, C212, C231, C232: 100n 100V X7; C_0603_1608Metric_Pad1.08x0.95mm_HandSolder; PartNumber TCC0603X7R104K101CT
C103, C104, C105, C106, C107, C108, C109, C110, C115, C116, C117, C118, C119, C120, C125, C126, C127, C128, C129, C131, C134, C135, C137, C138, C139, C140, C141, C142, C148, C149, C150, C151, C152, C153, C155, C156, C157, C159, C160, C161, C162, C164, C169, C170, C171, C172, C174, C175, C177, C178, C179, C180, C182, C183, C184, C186, C191, C192, C193, C194, C195, C196, C198, C199, C200, C201, C203, C204, C206, C207, C208, C213, C214, C215, C216, C217, C218, C221, C222, C225, C227, C228, C229, C230: 4.7u 100V X7; C_1210_3225Metric_Pad1.33x2.70mm_HandSolder; PartNumber HMK325C7475KMHPE
H101, H102, H103, H104, H105, H106, H107, H108: M3; MountingHole_3.2mm_M3

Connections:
+BATT: C101.1, C102.1, C103.1, C104.1, C105.1, C106.1, C107.1, C108.1, C109.1, C110.1, C115.1, C116.1, C117.1, C118.1, C119.1, C120.1, C121.1, C122.1, C123.1, C124.1, C125.1, C126.1, C127.1, C128.1, C129.1, C131.1, C134.1, C135.1, C137.1, C138.1, C139.1, C140.1, C141.1, C142.1, C143.1, C144.1, C145.1, C146.1, C148.1, C149.1, C150.1, C151.1, C152.1, C153.1, C155.1, C156.1, C157.1, C159.1, C160.1, C161.1, C162.1, C164.1, C165.1, C166.1, C167.1, C168.1, C169.1, C170.1, C171.1, C172.1, C174.1, C175.1, C177.1, C178.1, C179.1, C180.1, C182.1, C183.1, C184.1, C186.1, C187.1, C188.1, C189.1, C190.1, C191.1, C192.1, C193.1, C194.1, C195.1, C196.1, C198.1, C199.1, C200.1, C201.1, C203.1, C204.1, C206.1, C207.1, C208.1, C209.1, C210.1, C211.1, C212.1, C213.1, C214.1, C215.1, C216.1, C217.1, C218.1, C221.1, C222.1, C225.1, C227.1, C228.1, C229.1, C230.1, C231.1, C232.1
-BATT: C101.2, C102.2, C103.2, C104.2, C105.2, C106.2, C107.2, C108.2, C109.2, C110.2, C115.2, C116.2, C117.2, C118.2, C119.2, C120.2, C121.2, C122.2, C123.2, C124.2, C125.2, C126.2, C127.2, C128.2, C129.2, C131.2, C134.2, C135.2, C137.2, C138.2, C139.2, C140.2, C141.2, C142.2, C143.2, C144.2, C145.2, C146.2, C148.2, C149.2, C150.2, C151.2, C152.2, C153.2, C155.2, C156.2, C157.2, C159.2, C160.2, C161.2, C162.2, C164.2, C165.2, C166.2, C167.2, C168.2, C169.2, C170.2, C171.2, C172.2, C174.2, C175.2, C177.2, C178.2, C179.2, C180.2, C182.2, C183.2, C184.2, C186.2, C187.2, C188.2, C189.2, C190.2, C191.2, C192.2, C193.2, C194.2, C195.2, C196.2, C198.2, C199.2, C200.2, C201.2, C203.2, C204.2, C206.2, C207.2, C208.2, C209.2, C210.2, C211.2, C212.2, C213.2, C214.2, C215.2, C216.2, C217.2, C218.2, C221.2, C222.2, C225.2, C227.2, C228.2, C229.2, C230.2, C231.2, C232.2

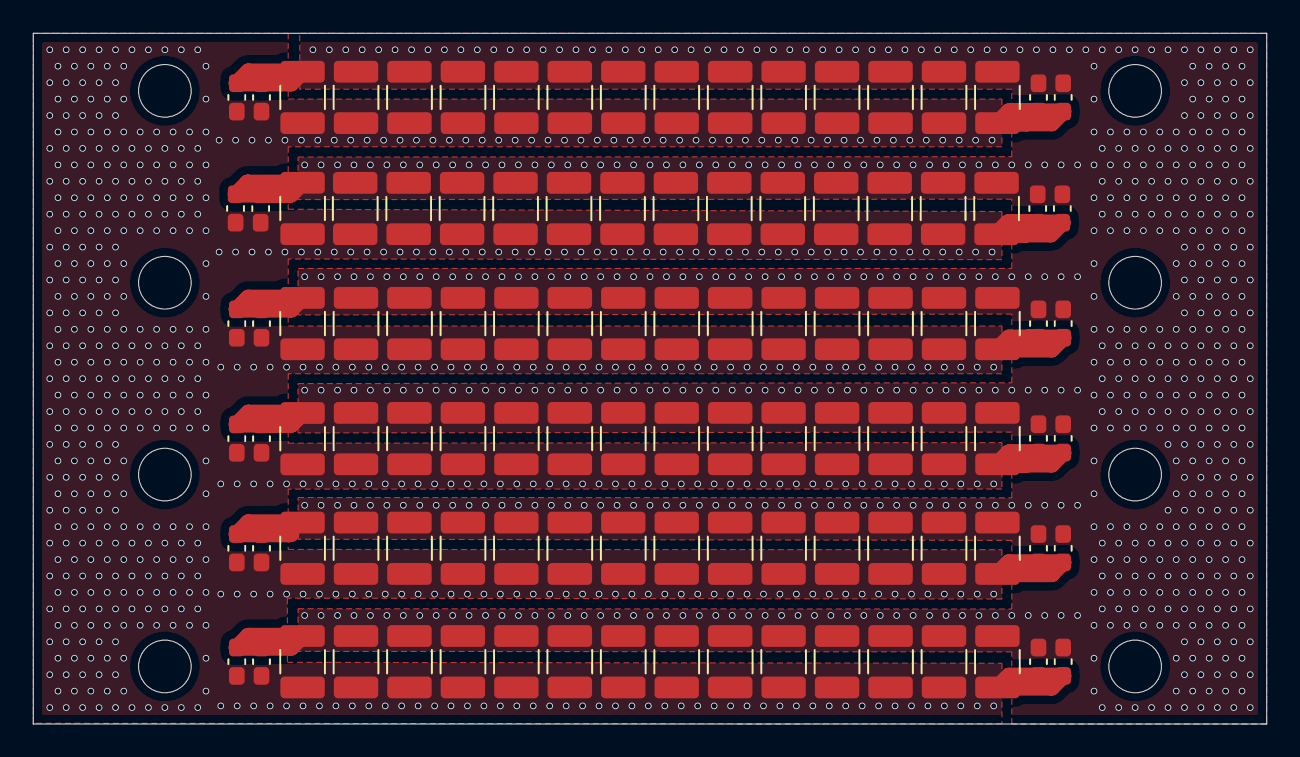
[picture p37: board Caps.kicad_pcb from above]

Board: 2 copper layers, 75.0 x 42.0 mm, 116 parts (0 on the bottom side), 2 nets.

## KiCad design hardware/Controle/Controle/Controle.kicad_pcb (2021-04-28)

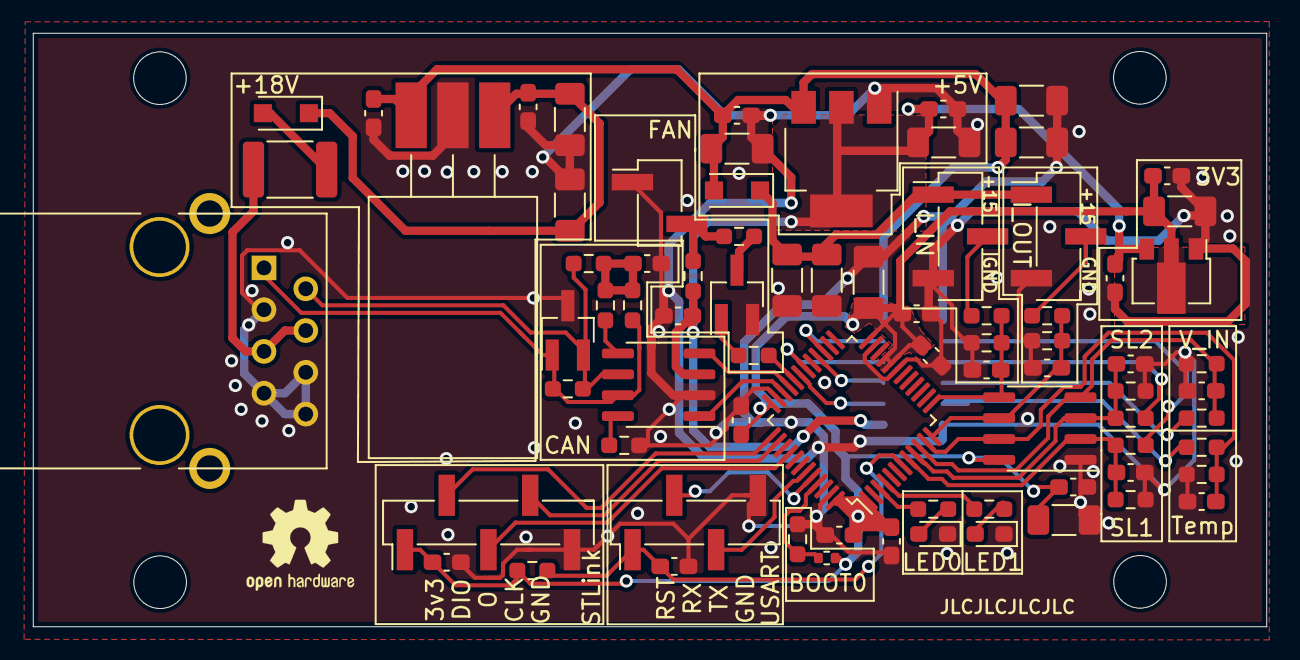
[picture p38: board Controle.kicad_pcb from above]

Board: 2 copper layers, 75.0 x 36.1 mm, 82 parts (1 on the bottom side), 46 nets.

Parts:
C1, C2, C3, C4, C5, C6, C7, C12, C102, C103, C104: 4.7u; C_1206_3216Metric_Pad1.33x1.80mm_HandSolder
C8, C9, C10, C11, C101, C201, C401, C402, C403, C404, C405, C406, C503, C504, C604, C607: 100n; C_0603_1608Metric_Pad1.08x0.95mm_HandSolder
C202: 4.7n; C_0603_1608Metric_Pad1.08x0.95mm_HandSolder
C601, C602, C603: 1n; C_0603_1608Metric_Pad1.08x0.95mm_HandSolder
C605, C606: NC; C_0603_1608Metric_Pad1.08x0.95mm_HandSolder
D101, D102: B0530W; D_SOD-123F
D201: pesd1can; SOT-23_Handsoldering
D501: B; LED_0603_1608Metric_Pad1.05x0.95mm_HandSolder
D502: G; LED_0603_1608Metric_Pad1.05x0.95mm_HandSolder
F101: 1A; Fuse_1812_4532Metric_Pad1.30x3.40mm_HandSolder
H101, H102, H103, H104: MountingHole; MountingHole_3.2mm_M3
J101: USART; PinHeader_1x04_P2.54mm_Vertical_SMD_Pin1Left
J102: ST_LINK; PinHeader_1x05_P2.54mm_Vertical_SMD_Pin1Left
J103: FAN; PinHeader_1x02_P2.54mm_Vertical_SMD_Pin1Left
J105, J106: Iin_sen; PinHeader_1x03_P2.54mm_Vertical_SMD_Pin1Left
J107: Driver-Sense; PinSocket_2x10_P1.27mm_Vertical_SMD
J301: RJ45; RJ45_YH59_01
Q101: BCV27; SOT-23_Handsoldering
R101, R102: 100R; R_0603_1608Metric_Pad0.98x0.95mm_HandSolder
R103, R501, R502, R503, R505, R601, R602, R603: 10k; R_0603_1608Metric_Pad0.98x0.95mm_HandSolder
R201: 4k7; R_0603_1608Metric_Pad0.98x0.95mm_HandSolder
R202: 1k; R_0603_1608Metric_Pad0.98x0.95mm_HandSolder
R203: 300; R_0603_1608Metric_Pad0.98x0.95mm_HandSolder
R204, R205: 60; R_0603_1608Metric_Pad0.98x0.95mm_HandSolder
R504: BOOT0; R_0402_1005Metric
R604: 0R; R_0603_1608Metric_Pad0.98x0.95mm_HandSolder
R605, R606, R610, R611, R612: NC; R_0603_1608Metric_Pad0.98x0.95mm_HandSolder
R607, R608, R609: 3k3; R_0603_1608Metric_Pad0.98x0.95mm_HandSolder
U201: MCP2561-E-SN; SOIC-8_3.9x4.9mm_P1.27mm
U401: AMS1117-3.3; SOT-89-3
U402: AMS1117-5; SOT-223-3_TabPin2
U403: K78L15-1000R3; TO-220-3_Horizontal_Tabless_SMD
U501: STM32G431CBT6; LQFP-48_7x7mm_P0.5mm
U601: TL7726IDR; SOIC-8_3.9x4.9mm_P1.27mm

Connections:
+3V3: C2.2, C7.2, C8.2, C9.2, C10.2, C11.2, C12.2, C101.2, C401.2, C504.2, C607.2, J102.1, R501.2, R504.1, U401.2, U501.1, U501.20, U501.21, U501.24, U501.36, U501.48, U601.8
+5V: C3.2, C201.2, C402.2, C403.2, J107.19, R103.2, U201.3, U401.3, U402.2
+15V: C1.2, C4.2, C104.2, C404.2, C405.2, D102.2, J107.1, J107.3, J107.5, J107.7, J107.9, U402.3, U403.3
/Iin_sen: J106.2, R605.2
/Iout_sen: J105.2, R606.2
/PWM_H1: J107.13, U501.30
/PWM_H2: J107.17, U501.31
/PWM_L1: J107.11, U501.27
/PWM_L2: J107.15, U501.28
/Powersupply/+18V: C5.2, C6.2, C406.2, D101.1, U403.1
/SL1_sen: J107.12, R601.2
/SL2_sen: J107.14, R602.2
/STM32/ADC1_IN0: C601.1, R601.1, R607.2, U501.8, U601.2
/STM32/ADC1_IN1: C602.1, R602.1, R608.2, U501.9, U601.3
/STM32/ADC1_IN2: C603.1, R603.1, R609.2, U501.10, U601.4
/STM32/ADCX_IN3: C604.1, R604.1, R610.2, U501.11, U601.7
/STM32/ADCX_IN4: C605.1, R605.1, R611.2, U501.12, U601.6
/STM32/ADCX_IN5: C606.1, R606.1, R612.2, U501.13, U601.5
/STM32/BOOT0: R504.2, R505.1, U501.45
/STM32/CAN_RX: U201.4, U501.33
/STM32/CAN_TX: U201.1, U501.34
/STM32/FAN: R102.1, U501.32
/STM32/LED0: R502.1, U501.3
/STM32/LED1: R503.1, U501.4
/STM32/RESET: C503.2, J101.1, R501.1, U501.7
/STM32/SWCLK: J102.4, U501.38
/STM32/SWDIO: J102.2, U501.37
/STM32/SWO: J102.3, U501.40
/STM32/USART3_RX: J101.2, U501.44
/STM32/USART3_TX: J101.3, U501.43
/Temp1: J107.18, R604.2
/Vin_sen: J107.16, R603.2
/canbus/CAN_H: D201.1, J301.1, R202.2, R204.2, U201.7
/canbus/CAN_L: D201.2, J301.2, R202.1, R205.1, U201.6
/canbus_connector/CAN_18V: F101.2, J301.4, J301.5
GND: C1.1, C2.1, C3.1, C4.1, C5.1, C6.1, C7.1, C8.1, C9.1, C10.1, C11.1, C12.1, C101.1, C102.1, C103.1, C104.1, C201.1, C202.2, C401.1, C402.1, C403.1, C404.1, C405.1, C406.1, C503.1, C504.1, C601.2, C602.2, C603.2, C604.2, C605.2, C606.2, C607.1, D201.3, D501.1, D502.1, J101.4, J102.5, J103.1, J105.3, J106.3, J107.2, J107.4, J107.6, J107.8, J107.10, J107.20, J301.3, J301.6, J301.7, J301.8, Q101.2, R201.2, R505.2, R607.1, R608.1, R609.1, R610.1, R611.1, R612.1, U201.2, U401.1, U402.1, U403.2, U501.19, U501.23, U501.35, U501.47, U601.1
unnamed: C102.2, C103.2, D102.1, J105.1, J106.1
unnamed: C202.1, R203.1, R204.1, R205.2
unnamed: D101.2, F101.1
unnamed: D501.2, R502.2
unnamed: D502.2, R503.2
unnamed: J103.2, R101.2, R103.1
unnamed: Q101.1, R102.2
unnamed: Q101.3, R101.1
unnamed: R201.1, U201.8
unnamed: R203.2, U201.5

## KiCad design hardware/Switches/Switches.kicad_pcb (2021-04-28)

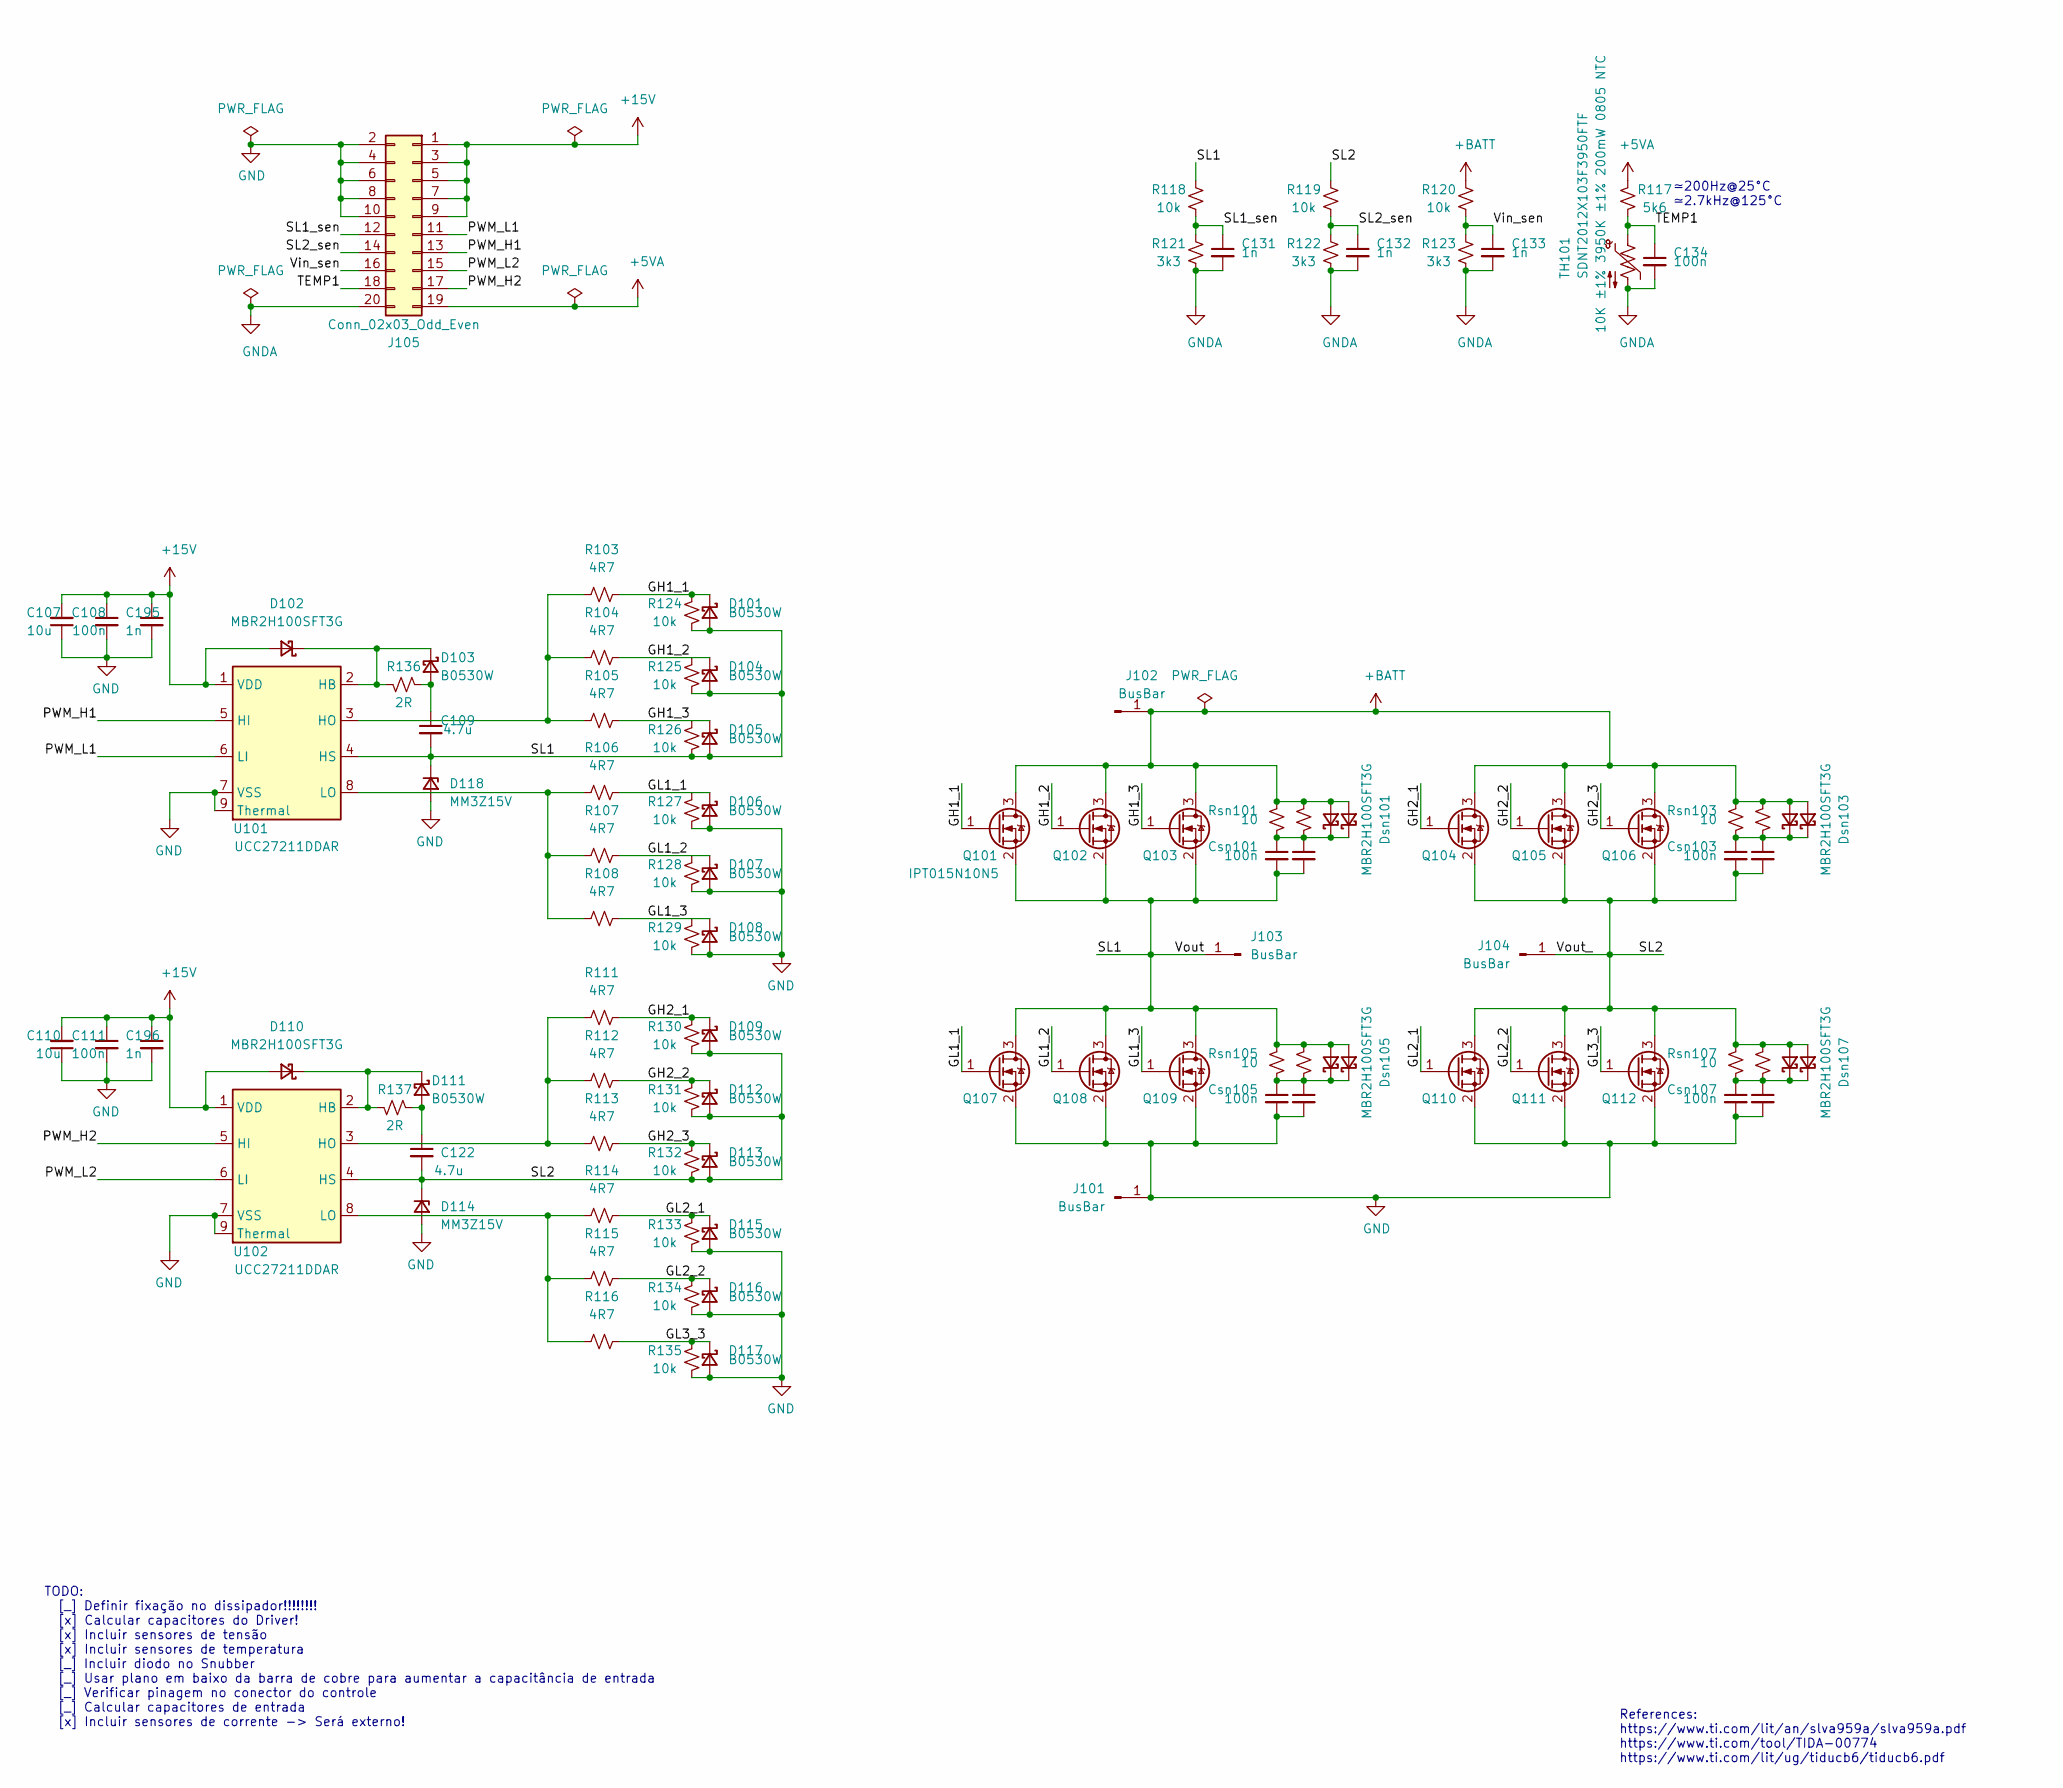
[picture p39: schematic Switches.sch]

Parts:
C107, C110: 10u; C_1210_3225Metric_Pad1.33x2.70mm_HandSolder
C108, C111: 100n; C_0805_2012Metric_Pad1.18x1.45mm_HandSolder
C109, C122: 4.7u; C_1210_3225Metric_Pad1.33x2.70mm_HandSolder
C131, C132, C133, C195, C196: 1n; C_0603_1608Metric_Pad1.08x0.95mm_HandSolder
C134: 100n; C_0603_1608Metric_Pad1.08x0.95mm_HandSolder
Csn101, Csn103, Csn105, Csn107: 100n; C_1210_3225Metric_Pad1.33x2.70mm_HandSolder
Csn102, Csn104, Csn106, Csn108: NC; C_1210_3225Metric_Pad1.33x2.70mm_HandSolder
D101, D103, D104, D105, D106, D107, D108, D109, D111, D112, D113, D115, D116, D117: B0530W; D_SOD-123F
D102, D110: MBR2H100SFT3G; D_SOD-123F
D114, D118: MM3Z15V; D_SOD-323
Dsn101, Dsn103, Dsn105, Dsn107: MBR2H100SFT3G; D_SOD-123F
Dsn102, Dsn104, Dsn106, Dsn108: NC; D_SOD-123F
J101, J102: BusBar; BusBar1
J103, J104: BusBar; BusBar2
J105: Conn_02x03_Odd_Even; PinHeader_2x10_P1.27mm_Vertical_SMD
Q101, Q102, Q103, Q104, Q105, Q106, Q107, Q108, Q109, Q110, Q111, Q112: IPT015N10N5; Infineon_PG-HSOF-8-1_ThermalVias3
R103, R104, R105, R106, R107, R108, R111, R112, R113, R114, R115, R116: 4R7; R_0805_2012Metric_Pad1.20x1.40mm_HandSolder
R117: 5k6; R_0603_1608Metric_Pad0.98x0.95mm_HandSolder
R118, R119, R120, R124, R125, R126, R127, R128, R129, R130, R131, R132, R133, R134, R135: 10k; R_0603_1608Metric_Pad0.98x0.95mm_HandSolder
R121, R122, R123: 3k3; R_0603_1608Metric_Pad0.98x0.95mm_HandSolder
R136, R137: 2R; R_0603_1608Metric_Pad0.98x0.95mm_HandSolder
Rsn101, Rsn103, Rsn105, Rsn107: 10; R_1210_3225Metric_Pad1.30x2.65mm_HandSolder
Rsn102, Rsn104, Rsn106, Rsn108: NC; R_1210_3225Metric_Pad1.30x2.65mm_HandSolder
TH101: SDNT2012X103F3950FTF; R_0805_2012Metric_Pad1.20x1.40mm_HandSolder
U101, U102: UCC27211DDAR; SOIC-8-1EP_3.9x4.9mm_P1.27mm_EP2.514x3.2mm_ThermalVias

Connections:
+5VA: J105.19, R117.1
+15V: C107.2, C108.1, C110.2, C111.1, C195.1, C196.1, D102.2 (A), D110.2 (A), J105.1, J105.3, J105.5, J105.7, J105.9, U101.1 (VDD), U102.1 (VDD)
+BATT: Dsn101.2 (A), Dsn102.2 (A), Dsn103.2 (A), Dsn104.2 (A), J102.1, Q101.3 (D), Q102.3 (D), Q103.3 (D), Q104.3 (D), Q105.3 (D), Q106.3 (D), R120.1, Rsn101.1, Rsn102.1, Rsn103.1, Rsn104.1
/GH1_1: D101.1 (K), Q101.1 (G), R103.1, R124.2
/GH1_2: D104.1 (K), Q102.1 (G), R104.1, R125.2
/GH1_3: D105.1 (K), Q103.1 (G), R105.1, R126.2
/GH2_1: D109.1 (K), Q104.1 (G), R111.1, R130.2
/GH2_2: D112.1 (K), Q105.1 (G), R112.1, R131.2
/GH2_3: D113.1 (K), Q106.1 (G), R113.1, R132.2
/GL1_1: D106.1 (K), Q107.1 (G), R106.1, R127.2
/GL1_2: D107.1 (K), Q108.1 (G), R107.1, R128.2
/GL1_3: D108.1 (K), Q109.1 (G), R108.1, R129.2
/GL2_1: D115.1 (K), Q110.1 (G), R114.1, R133.2
/GL2_2: D116.1 (K), Q111.1 (G), R115.1, R134.2
/GL3_3: D117.1 (K), Q112.1 (G), R116.1, R135.2
/PWM_H1: J105.13, U101.5 (HI)
/PWM_H2: J105.17, U102.5 (HI)
/PWM_L1: J105.11, U101.6 (LI)
/PWM_L2: J105.15, U102.6 (LI)
/SL1: C109.2, Csn101.2, Csn102.2, D101.2 (A), D104.2 (A), D105.2 (A), D118.1 (K), Dsn105.2 (A), Dsn106.2 (A), J103.1, Q101.2 (S), Q102.2 (S), Q103.2 (S), Q107.3 (D), Q108.3 (D), Q109.3 (D), R118.1, R124.1, R125.1, R126.1, Rsn105.1, Rsn106.1, U101.4 (HS)
/SL1_sen: C131.1, J105.12, R118.2, R121.1
/SL2: C122.2, Csn103.2, Csn104.2, D109.2 (A), D112.2 (A), D113.2 (A), D114.1 (K), Dsn107.2 (A), Dsn108.2 (A), J104.1, Q104.2 (S), Q105.2 (S), Q106.2 (S), Q110.3 (D), Q111.3 (D), Q112.3 (D), R119.1, R130.1, R131.1, R132.1, Rsn107.1, Rsn108.1, U102.4 (HS)
/SL2_sen: C132.1, J105.14, R119.2, R122.1
/TEMP1: C134.1, J105.18, R117.2, TH101.1
/Vin_sen: C133.1, J105.16, R120.2, R123.1
GND: C107.1, C108.2, C110.1, C111.2, C195.2, C196.2, Csn105.2, Csn106.2, Csn107.2, Csn108.2, D106.2 (A), D107.2 (A), D108.2 (A), D114.2 (A), D115.2 (A), D116.2 (A), D117.2 (A), D118.2 (A), J101.1, J105.2, J105.4, J105.6, J105.8, J105.10, Q107.2 (S), Q108.2 (S), Q109.2 (S), Q110.2 (S), Q111.2 (S), Q112.2 (S), R127.1, R128.1, R129.1, R133.1, R134.1, R135.1, U101.7 (VSS), U101.9 (Thermal), U102.7 (VSS), U102.9 (Thermal)
GNDA: C131.2, C132.2, C133.2, C134.2, J105.20, R121.2, R122.2, R123.2, TH101.2
unnamed: C109.1, D103.2 (A), R136.2
unnamed: C122.1, D111.2 (A), R137.2
unnamed: Csn101.1, Csn102.1, Dsn101.1 (K), Dsn102.1 (K), Rsn101.2, Rsn102.2
unnamed: Csn103.1, Csn104.1, Dsn103.1 (K), Dsn104.1 (K), Rsn103.2, Rsn104.2
unnamed: Csn105.1, Csn106.1, Dsn105.1 (K), Dsn106.1 (K), Rsn105.2, Rsn106.2
unnamed: Csn107.1, Csn108.1, Dsn107.1 (K), Dsn108.1 (K), Rsn107.2, Rsn108.2
unnamed: D102.1 (K), D103.1 (K), R136.1, U101.2 (HB)
unnamed: D110.1 (K), D111.1 (K), R137.1, U102.2 (HB)
unnamed: R103.2, R104.2, R105.2, U101.3 (HO)
unnamed: R106.2, R107.2, R108.2, U101.8 (LO)
unnamed: R111.2, R112.2, R113.2, U102.3 (HO)
unnamed: R114.2, R115.2, R116.2, U102.8 (LO)

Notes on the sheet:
TODO: [_] Definir fixação no dissipador!!!!!!!! [x] Calcular capacitores do Driver! [x] Incluir sensores de tensão [x] Incluir sensores de temperatura [_] Incluir diodo no Snubber [_] Usar plano em baixo da barra de cobre para aumentar a capacitância de entrada [_] Verificar pinagem no conector do 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
References: https://www.ti.com/lit/an/slva959a/slva959a.pdf https://www.ti.com/tool/TIDA-00774 https://www.ti.com/lit/ug/tiducb6/tiducb6.pdf
≃200Hz@25°C ≃2.7kHz@125°C

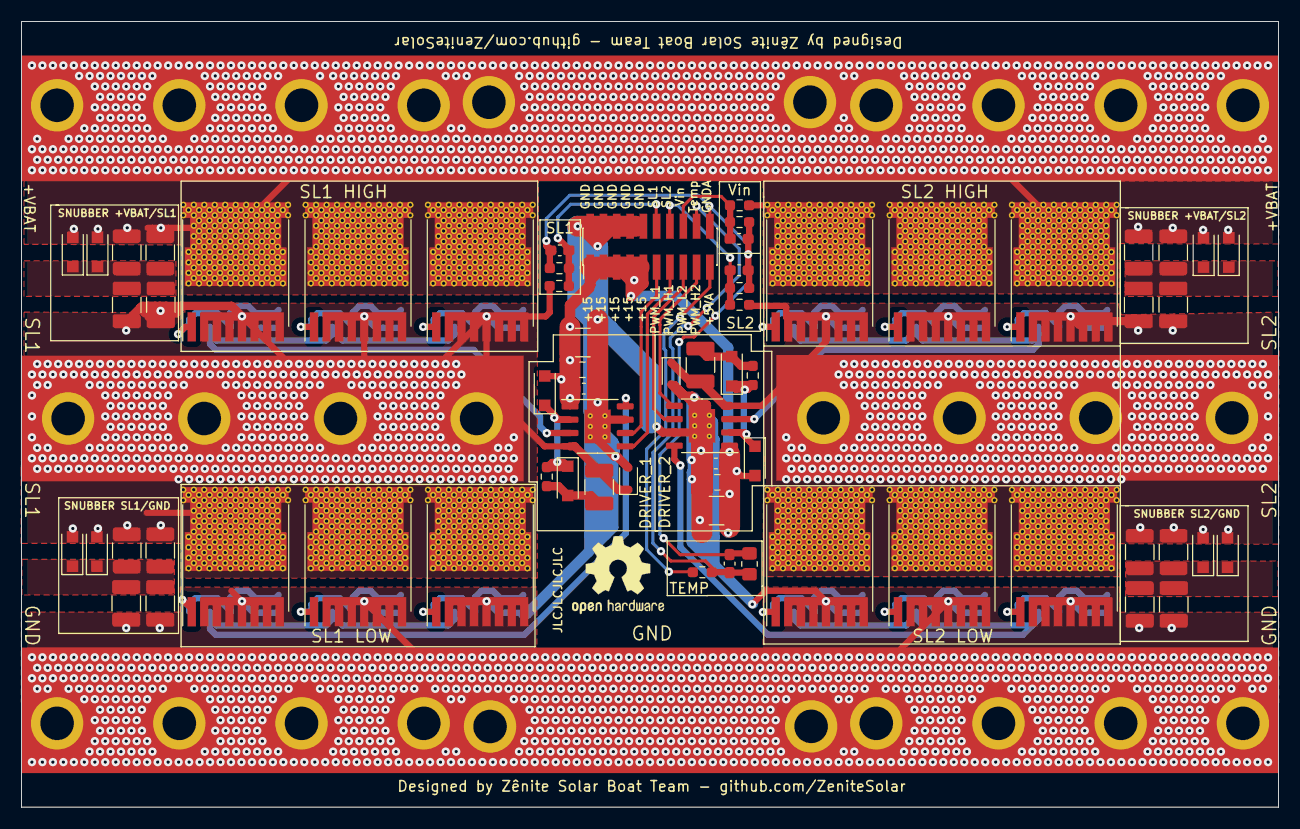
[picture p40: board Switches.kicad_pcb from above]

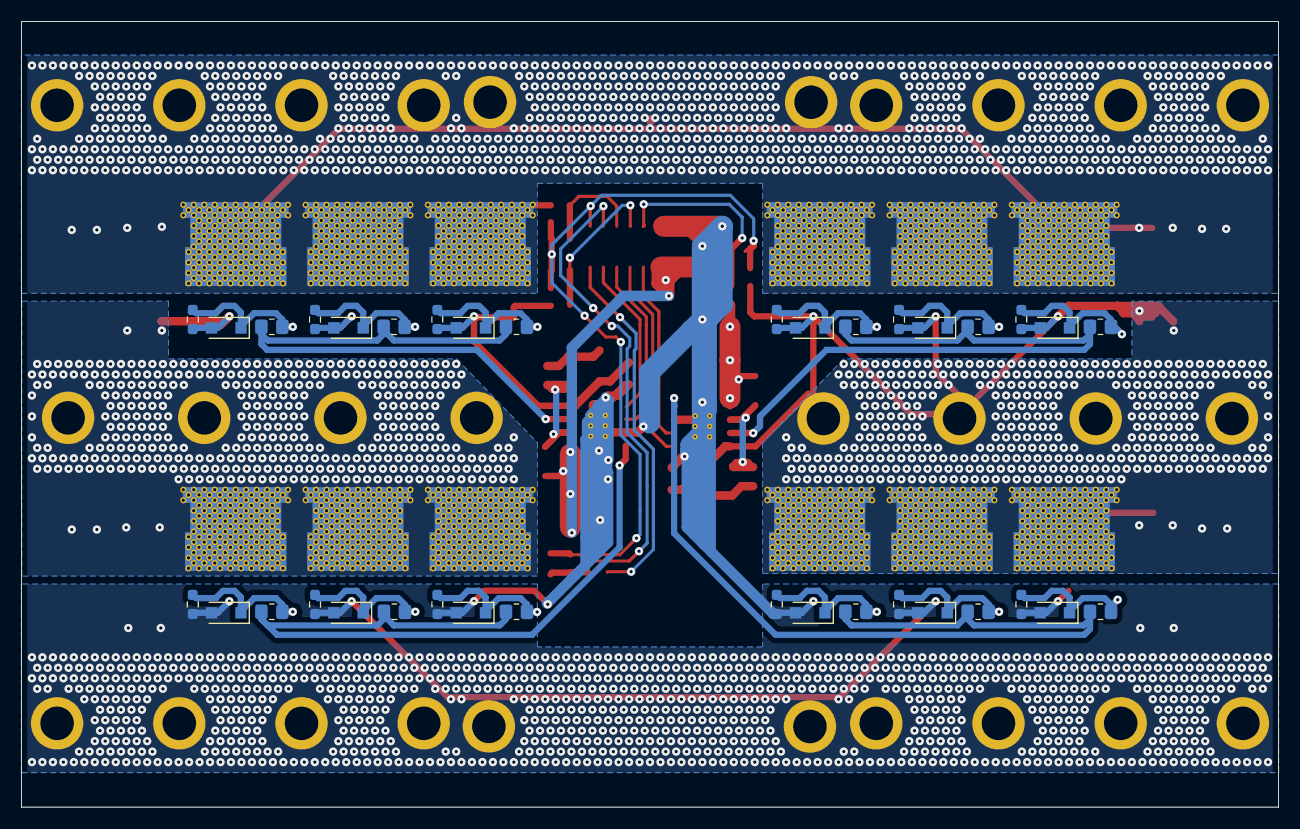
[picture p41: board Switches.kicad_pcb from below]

Board: 4 copper layers, 120.0 x 75.0 mm, 107 parts (36 on the bottom side), 39 nets.

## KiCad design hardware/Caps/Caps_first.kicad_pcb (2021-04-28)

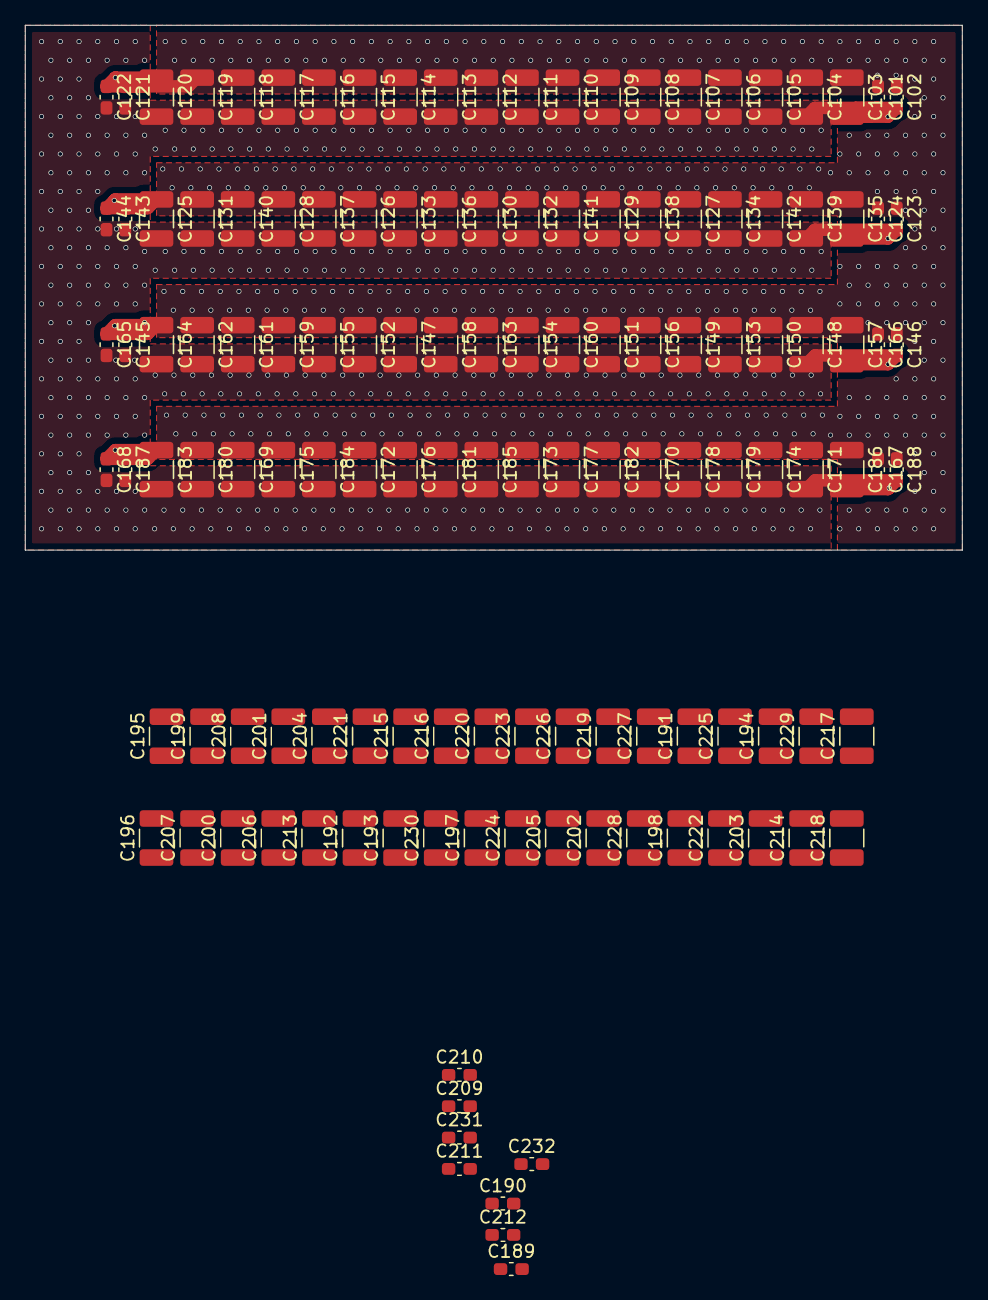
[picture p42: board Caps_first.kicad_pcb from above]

Board: 2 copper layers, 75.0 x 42.0 mm, 132 parts (0 on the bottom side), 2 nets.

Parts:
C101, C102, C121, C122, C123, C124, C143, C144, C145, C146, C165, C166, C167, C168, C187, C188, C189, C190, C209, C210, C211, C212, C231, C232: 100n 100V X7; C_0603_1608Metric_Pad1.08x0.95mm_HandSolder
C103, C104, C105, C106, C107, C108, C109, C110, C111, C112, C113, C114, C115, C116, C117, C118, C119, C120, C125, C126, C127, C128, C129, C130, C131, C132, C133, C134, C135, C136, C137, C138, C139, C140, C141, C142, C147, C148, C149, C150, C151, C152, C153, C154, C155, C156, C157, C158, C159, C160, C161, C162, C163, C164, C169, C170, C171, C172, C173, C174, C175, C176, C177, C178, C179, C180, C181, C182, C183, C184, C185, C186, C191, C192, C193, C194, C195, C196, C197, C198, C199, C200, C201, C202, C203, C204, C205, C206, C207, C208, C213, C214, C215, C216, C217, C218, C219, C220, C221, C222, C223, C224, C225, C226, C227, C228, C229, C230: 4.7u 100V X7; C_1210_3225Metric_Pad1.33x2.70mm_HandSolder

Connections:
+BATT: C101.1, C102.1, C103.1, C104.1, C105.1, C106.1, C107.1, C108.1, C109.1, C110.1, C111.1, C112.1, C113.1, C114.1, C115.1, C116.1, C117.1, C118.1, C119.1, C120.1, C121.1, C122.1, C123.1, C124.1, C125.1, C126.1, C127.1, C128.1, C129.1, C130.1, C131.1, C132.1, C133.1, C134.1, C135.1, C136.1, C137.1, C138.1, C139.1, C140.1, C141.1, C142.1, C143.1, C144.1, C145.1, C146.1, C147.1, C148.1, C149.1, C150.1, C151.1, C152.1, C153.1, C154.1, C155.1, C156.1, C157.1, C158.1, C159.1, C160.1, C161.1, C162.1, C163.1, C164.1, C165.1, C166.1, C167.1, C168.1, C169.1, C170.1, C171.1, C172.1, C173.1, C174.1, C175.1, C176.1, C177.1, C178.1, C179.1, C180.1, C181.1, C182.1, C183.1, C184.1, C185.1, C186.1, C187.1, C188.1, C189.1, C190.1, C191.1, C192.1, C193.1, C194.1, C195.1, C196.1, C197.1, C198.1, C199.1, C200.1, C201.1, C202.1, C203.1, C204.1, C205.1, C206.1, C207.1, C208.1, C209.1, C210.1, C211.1, C212.1, C213.1, C214.1, C215.1, C216.1, C217.1, C218.1, C219.1, C220.1, C221.1, C222.1, C223.1, C224.1, C225.1, C226.1, C227.1, C228.1, C229.1, C230.1, C231.1, C232.1
-BATT: C101.2, C102.2, C103.2, C104.2, C105.2, C106.2, C107.2, C108.2, C109.2, C110.2, C111.2, C112.2, C113.2, C114.2, C115.2, C116.2, C117.2, C118.2, C119.2, C120.2, C121.2, C122.2, C123.2, C124.2, C125.2, C126.2, C127.2, C128.2, C129.2, C130.2, C131.2, C132.2, C133.2, C134.2, C135.2, C136.2, C137.2, C138.2, C139.2, C140.2, C141.2, C142.2, C143.2, C144.2, C145.2, C146.2, C147.2, C148.2, C149.2, C150.2, C151.2, C152.2, C153.2, C154.2, C155.2, C156.2, C157.2, C158.2, C159.2, C160.2, C161.2, C162.2, C163.2, C164.2, C165.2, C166.2, C167.2, C168.2, C169.2, C170.2, C171.2, C172.2, C173.2, C174.2, C175.2, C176.2, C177.2, C178.2, C179.2, C180.2, C181.2, C182.2, C183.2, C184.2, C185.2, C186.2, C187.2, C188.2, C189.2, C190.2, C191.2, C192.2, C193.2, C194.2, C195.2, C196.2, C197.2, C198.2, C199.2, C200.2, C201.2, C202.2, C203.2, C204.2, C205.2, C206.2, C207.2, C208.2, C209.2, C210.2, C211.2, C212.2, C213.2, C214.2, C215.2, C216.2, C217.2, C218.2, C219.2, C220.2, C221.2, C222.2, C223.2, C224.2, C225.2, C226.2, C227.2, C228.2, C229.2, C230.2, C231.2, C232.2

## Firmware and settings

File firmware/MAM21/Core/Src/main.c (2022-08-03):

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
/* Includes ------------------------------------------------------------------*/
#include "main.h"

/* USER CODE BEGIN Includes */
#include "machine.h"
/* USER CODE END Includes */

ADC_HandleTypeDef hadc1;
ADC_HandleTypeDef hadc2;

FDCAN_HandleTypeDef hfdcan1;

TIM_HandleTypeDef htim1;
TIM_HandleTypeDef htim2;
TIM_HandleTypeDef htim16;
TIM_HandleTypeDef htim17;

UART_HandleTypeDef huart1;

/* USER CODE BEGIN PV */
uint8_t batata;
uint8_t ubKeyNumber = 0x0;
FDCAN_RxHeaderTypeDef RxHeader;
FDCAN_TxHeaderTypeDef TxHeader;


// For PWM control of engine
struct MotorControl
{
    uint32_t dir;
    uint32_t enable;
    float duty;
} control_temp;

/* USER CODE END PV */

void SystemClock_Config(void);
static void MX_GPIO_Init(void);
static void MX_ADC1_Init(void);
static void MX_ADC2_Init(void);
static void MX_FDCAN1_Init(void);
static void MX_USART1_UART_Init(void);
static void MX_TIM2_Init(void);
static void MX_TIM16_Init(void);
static void MX_TIM17_Init(void);
static void MX_TIM1_Init(void);
/* USER CODE BEGIN PFP */
static void FDCAN_Config(void);
/* USER CODE END PFP */

/**
 * @brief  The application entry point.
 * @retval int
 */
int main(void)
{
    /* MCU Configuration--------------------------------------------------------*/

    /* Reset of all peripherals, Initializes the Flash interface and the Systick. */
    HAL_Init();

    /* Configure the system clock */
    SystemClock_Config();

    /* Initialize all configured peripherals */
    MX_GPIO_Init();
    MX_ADC1_Init();
    MX_ADC2_Init();
    MX_FDCAN1_Init();
    MX_USART1_UART_Init();
    MX_TIM2_Init();
    MX_TIM16_Init();
    MX_TIM17_Init();
    MX_TIM1_Init();
    /* USER CODE BEGIN 2 */
    /* Configure the FDCAN peripheral */
    FDCAN_Config();
    machine_init();
    control_init(&htim1);
    /* USER CODE END 2 */

    /* Infinite loop */
    /* USER CODE BEGIN WHILE */
    while (1)
    {
        /* USER CODE END WHILE */

        /* USER CODE BEGIN 3 */
        /* Set the data to be transmitted */

        // batata = HAL_FDCAN_GetRxFifoFillLevel(&hfdcan1, FDCAN_RX_FIFO0);
        // /* Start the Transmission process */
        // if (HAL_FDCAN_AddMessageToTxFifoQ(&hfdcan1, &TxHeader, TxData) != HAL_OK)
        // {
        //     /* Transmission request Error */
        //     //  Error_Handler();
        // }
        /* Retrieve Rx messages from RX FIFO0 */

        // HAL_FDCAN_IRQHandler(&hfdcan1);
        
        machine_run();
    }
    /* USER CODE END 3 */
}

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
/* USER CODE BEGIN 4 */
static void FDCAN_Config(void)
{
    FDCAN_FilterTypeDef sFilterConfig;

    /* Configure Rx filter */
    sFilterConfig.IdType = FDCAN_STANDARD_ID;
    sFilterConfig.FilterIndex = 0;
    sFilterConfig.FilterType = FDCAN_FILTER_MASK;
    sFilterConfig.FilterConfig = FDCAN_FILTER_TO_RXFIFO0;
    sFilterConfig.FilterID1 = 0x00;
    sFilterConfig.FilterID2 = 0x00;
    if (HAL_FDCAN_ConfigFilter(&hfdcan1, &sFilterConfig) != HAL_OK)
    {
        Error_Handler();
    }

    /* Configure global filter:
      Filter all remote frames with STD and EXT ID
      Reject non matching frames with STD ID and EXT ID */
    if (HAL_FDCAN_ConfigGlobalFilter(&hfdcan1, FDCAN_REJECT, FDCAN_REJECT, FDCAN_FILTER_REMOTE, FDCAN_FILTER_REMOTE) != HAL_OK)
    {
        Error_Handler();
    }

    /* Start the FDCAN module */
    if (HAL_FDCAN_Start(&hfdcan1) != HAL_OK)
    {
        Error_Handler();
    }

    if (HAL_FDCAN_ActivateNotification(&hfdcan1, FDCAN_IT_RX_FIFO0_NEW_MESSAGE, 0) != HAL_OK)
    {
        Error_Handler();
    }
    if (HAL_FDCAN_ActivateNotification(&hfdcan1, FDCAN_IT_RX_FIFO1_NEW_MESSAGE, 0) != HAL_OK)
    {
        Error_Handler();
    }

    /* Prepare Tx Header */
    TxHeader.Identifier = 0x321;
    TxHeader.IdType = FDCAN_STANDARD_ID;
    TxHeader.TxFrameType = FDCAN_DATA_FRAME;
    TxHeader.DataLength = FDCAN_DLC_BYTES_2;
    TxHeader.ErrorStateIndicator = FDCAN_ESI_ACTIVE;
    TxHeader.BitRateSwitch = FDCAN_BRS_OFF;
    TxHeader.FDFormat = FDCAN_CLASSIC_CAN;
    TxHeader.TxEventFifoControl = FDCAN_NO_TX_EVENTS;
    TxHeader.MessageMarker = 0;
}

void HAL_FDCAN_RxFifo0Callback(FDCAN_HandleTypeDef *hfdcan, uint32_t RxFifo0ITs)
{
    can_msg_t Rx_msg;
    if ((RxFifo0ITs & FDCAN_IT_RX_FIFO0_NEW_MESSAGE) != RESET)
    {
        /* Retrieve Rx messages from RX FIFO0 */
        if (HAL_FDCAN_GetRxMessage(hfdcan, FDCAN_RX_FIFO0, &Rx_msg.RxHeader, Rx_msg.data.raw) != HAL_OK)
        {
            
        }
        can_parse(&Rx_msg);
     
        HAL_GPIO_TogglePin(GPIOC, GPIO_PIN_14);
    }
}


/*
https://www.modularcircuits.com/blog/articles/h-bridge-secrets/h-bridge-control/

  | 0cycle | 1cycle
Q1|DIR      |DT
Q2|!DIR     |!DT
Q3|!DT     |!DIR
Q4|DT      |DIR
Assuming Q1 = CH1,Q2 = !CH1 and Q3 = CH2,Q4 = !CH2
    | 0cycle | 1 cycle
CH1 |DIR     | DT
CH2 |!DT     | !DIR
For the power off state all Mosfets can be disabled and let the current be conduced for the body diode

*/
void HAL_TIM_PeriodElapsedCallback(TIM_HandleTypeDef *htim)
{
    static uint32_t machine_clk_div = 0; 
    HAL_GPIO_TogglePin(LED0_GPIO_Port, LED0_Pin);

    if (htim->Instance == htim1.Instance)
    {
        if (++machine_clk_div >= 10){
            machine_clk_div = 0;
            machine_set_run();
        }
        h_bridge_run();
    }
}
void HAL_TIM_PWM_PulseFinishedCallback(TIM_HandleTypeDef *htim)
{
}
/* USER CODE END 4 */
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


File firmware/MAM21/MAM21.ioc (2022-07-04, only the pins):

Mcu.UserName=STM32G431C8Tx
PA0.Signal=ADC1_IN1
PA1.Signal=ADC1_IN2
PA10.GPIO_Label=FAN
PA10.Signal=S_TIM2_CH4
PA11.Signal=FDCAN1_RX
PA12.Signal=FDCAN1_TX
PA13.Signal=SYS_JTMS-SWDIO
PA14.Signal=SYS_JTCK-SWCLK
PA2.Signal=ADC1_IN3
PA3.Signal=ADC1_IN4
PA6.Signal=ADC2_IN3
PA7.Signal=ADC2_IN4
PA8.Signal=S_TIM1_CH1
PA9.Signal=S_TIM1_CH2
PB13.Signal=TIM1_CH1N
PB14.Signal=TIM1_CH2N
PB3.Signal=SYS_JTDO-SWO
PB6.Signal=USART1_TX
PB7.Signal=USART1_RX
PB8-BOOT0.GPIO_Label=BOOT0
PB8-BOOT0.Signal=GPIO_Input
PC14-OSC32_IN.GPIO_Label=LED0
PC14-OSC32_IN.Signal=GPIO_Output
PC15-OSC32_OUT.GPIO_Label=LED1
PC15-OSC32_OUT.Signal=GPIO_Output
PG10-NRST.GPIO_Label=RESET
PG10-NRST.Signal=GPIO_Input

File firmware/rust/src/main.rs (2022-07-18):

#![no_main]
#![no_std]

mod utils;

use defmt::info;
use fugit::{ExtU32, HertzU32, NanosDurationU32};

// These lines are part of our setup for debug printing.
// use panic_halt as _;
// use panic_reset as _;
use defmt_rtt as _;
use panic_probe as _;

use cortex_m::{
    self,
    asm::delay,
    delay::{self, Delay},
    interrupt::{free, Mutex},
    peripheral::NVIC,
    prelude::_embedded_hal_blocking_delay_DelayMs,
};
use cortex_m_rt::entry;

use stm32_hal2::{
    self,
    clocks::{Clk48Src, Clocks, InputSrc, PllCfg, PllSrc},
    dma::{Dma, DmaChannel, DmaInterrupt},
    gpio::{Edge, OutputType, Pin, PinMode, Port, Pull},
    low_power,
    pac::{self, tim1::dtr2::DTAE_R},
    timer::{OutputCompare, TimChannel, Timer, TimerConfig, TimerInterrupt},
};
use utils::U32Ext;

#[entry]
fn main() -> ! {
    let mut cp = cortex_m::Peripherals::take().unwrap();
    let mut dp = pac::Peripherals::take().unwrap();

    // This line is required to prevent the debugger from disconnecting on entering WFI.
    #[cfg(debug_assertions)]
    stm32_hal2::debug_workaround();

    // Create an initial clock configuration that uses the MCU's internal oscillator (HSI),
    // sets the MCU to its maximum system clock speed.
    let clock_cfg = Clocks {
        input_src: InputSrc::Pll(PllSrc::Hsi),
        pll: PllCfg {
            enabled: true,
            pllr_en: true,
            pllq_en: true,
            pllp_en: true,
            divm: stm32_hal2::clocks::Pllm::Div1,
            divn: 20,
            divr: stm32_hal2::clocks::Pllr::Div2,
            divq: stm32_hal2::clocks::Pllr::Div2,
            divp: stm32_hal2::clocks::Pllr::Div2,
        },
        hclk_prescaler: stm32_hal2::clocks::HclkPrescaler::Div2,
        apb1_prescaler: stm32_hal2::clocks::ApbPrescaler::Div1,
        apb2_prescaler: stm32_hal2::clocks::ApbPrescaler::Div1,
        clk48_src: Clk48Src::Pllq,
        hse_bypass: true,
        security_system: false,
        hsi48_on: false,
        boost_mode: true,
    };

    // Write the clock configuration to the MCU. If you wish, you can modify `clocks` above
    // in accordance with [its docs](https://docs.rs/stm32-hal2/latest/stm32_hal2/clocks/index.html),
    // and the `clock_cfg` example.
    clock_cfg.setup().unwrap();

    // Setup a delay, based on the Cortex-m systick.
    let mut delay = Delay::new(cp.SYST, clock_cfg.systick());

    let mut pwm_timer = Timer::pwm_hbridge_config(&clock_cfg, dp.TIM1, 12500.hertz(), 200.nanos());
    pwm_timer.enable();

    let mut dir = false;
    let mut dt = 0.;

    let mut ddt = 0.01;
    let mut cycle = false;
    let ncycles = 5;
    let mut cycles = 0;
    loop {
        pwm_timer.set_pwm(dt, dir, cycle);

        dt += ddt;
        if dt >= 1. || dt <= 0. {
            ddt = -ddt;
            defmt::println!("pwm: {:#?}, {:#?}, {:#?}", dt, dir, cycle);
        }

        cycles += 1;
        if cycles == ncycles {
            cycles = 0;
            cycle = !cycle;
        }

        delay.delay_ms(1_000);
    }
}

trait HBridge {
    // https://github.com/David-OConnor/stm32-hal/tree/main/examples
    fn pwm_hbridge_config(
        clock_cfg: &Clocks,
        tim: pac::TIM1,
        freq: HertzU32,
        deadtime: NanosDurationU32,
    ) -> Self;
    fn set_pwm(&mut self, dt: f32, dir: bool, cycle: bool);
}

impl HBridge for Timer<pac::TIM1> {
    fn pwm_hbridge_config(
        clock_cfg: &Clocks,
        tim: pac::TIM1,
        freq: HertzU32,
        deadtime: NanosDurationU32,
    ) -> Self {
        // References:
        // [RM0440 pg.1077 - "Advanced-control timers"](https://www.st.com/resource/en/reference_manual/rm0440-stm32g4-series-advanced-armbased-32bit-mcus-stmicroelectronics.pdf)
        // [AN4013 pg.26 - "Advanced features for motor control"](https://www.st.com/resource/en/application_note/an4013-stm32-crossseries-timer-overview-stmicroelectronics.pdf)
        // https://github.com/magiczny-kacper/STM32-H-Bridge/blob/main/Core/Src/main.c

        // Set up a PWM pin, ref for Alternate functions: https://www.st.com/resource/en/datasheet/stm32g431kb.pdf, pg 61
        let _pwm_ch1 = Pin::new(Port::A, 8, PinMode::Alt(6));
        let _pwm_ch2 = Pin::new(Port::A, 9, PinMode::Alt(6));
        let _pwm_ch1_n = Pin::new(Port::B, 13, PinMode::Alt(6));
        let _pwm_ch2_n = Pin::new(Port::B, 14, PinMode::Alt(6));

        // Set up a PWM timer that will output to PA0, run at 2400Hz in edge-aligned mode,
        // count up, with a 50% duty cycle.
        let mut pwm_timer = Timer::new_tim1(
            tim,
            freq.raw() as f32,
            TimerConfig {
                auto_reload_preload: true,
                one_pulse_mode: false,
                update_request_source: stm32_hal2::timer::UpdateReqSrc::OverUnderFlow,
                alignment: stm32_hal2::timer::Alignment::Center2, // FIXME: check this!
                capture_compare_dma: stm32_hal2::timer::CaptureCompareDma::Ccx,
                direction: stm32_hal2::timer::CountDir::Up,
            },
            &clock_cfg,
        );

        pwm_timer
            .set_complementary_polarity(TimChannel::C1, stm32_hal2::timer::Polarity::ActiveHigh);
        pwm_timer
            .set_complementary_polarity(TimChannel::C2, stm32_hal2::timer::Polarity::ActiveHigh);

        pwm_timer.set_preload(TimChannel::C1, true);
        pwm_timer.set_preload(TimChannel::C2, true);

        pwm_timer.set_output_compare(TimChannel::C1, OutputCompare::Pwm2);
        pwm_timer.set_output_compare(TimChannel::C2, OutputCompare::Pwm1);

        let (dtg, ckd) = utils::calculate_deadtime(clock_cfg.sysclk().hertz(), deadtime);
        pwm_timer.regs.cr1.modify(|_r, w| w.ckd().variant(ckd));
        pwm_timer.regs.bdtr.modify(|_r, w| {
            w.dtg()
                .variant(dtg)
                .lock()
                .variant(0b00) // "Lock configuration": Level 0
                .ossi()
                .variant(false) // "Off-state selection for idle mode": Hi-Z
                .ossr()
                .variant(false) // "Off-state selection for Run mode": Hi-Z
                .bke()
                .variant(false) // "Break enable": Disabled
                .aoe() // "Automatic output enable": MOE only by software
                .variant(false)
                .moe()
                .variant(false) // "Main output enable":
        });

        pwm_timer
    }

    fn set_pwm(&mut self, dt: f32, dir: bool, cycle: bool) {
        let dt = if dt < 0. { 0. } else { dt };
        let dt = if dt > 1. { 1. } else { dt };

        let max_dt = self.get_max_duty();

        let dt = (dt * (max_dt as f32)) as u16;
        let dir = (if dir { 1 } else { 0 }) * max_dt;

        let dt1 = if cycle { dir } else { dt };
        let dt2 = if cycle { dt } else { dir };

        self.set_duty(TimChannel::C1, dt1);
        self.set_duty(TimChannel::C2, dt2);
    }
}
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

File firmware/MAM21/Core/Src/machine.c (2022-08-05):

#include "machine.h"
#include "utils.h"
#include "control.h"
#include "can_app.h"

/* Some global variables*/
static machine_t machine;
system_infos_t system_infos;
system_flags_t system_flags;
error_flags_t error_flags;

/*
**  PRIVATE FUNCTIONS
*/

static void set_state_initializing(void);
static void set_state_idle(void);
static void set_state_running(void);
static void set_state_error(void);

/*
 * States of the machine
 */
// Initialize the machine
static void task_initializing(void);
// In this state, the motor is waiting for the boot procedure
static void task_idle(void);
// In this state, the motor is ready to run
static void task_running(void);
// Error state
static void task_error(void);

// Checks if the motor potentiometer was in the minimum for a while
static void check_pot_zero(void);

static void set_state_initializing(void)
{
    LOG_INFO("==> STATE INITIALIZING");
    control_clear();
    machine.state = STATE_INITIALIZING;
}

static void set_state_idle(void)
{
    LOG_INFO("==> STATE IDLE");
    machine.state = STATE_IDLE;
}

static void set_state_running(void)
{
    LOG_INFO("==> STATE RUNNING");
    machine.state = STATE_RUNNING;
}
static void set_state_error(void)
{
    LOG_INFO("==> STATE ERROR");
    machine.state = STATE_ERROR;
}

static void check_pot_zero(void)
{
    static const float error_tolerance = 0.01f;
    static uint32_t pot_zero_clk;
    if (machine.motor.duty >= error_tolerance)
    {
        pot_zero_clk = 0;
    }

    if (++pot_zero_clk >= 10)
    {
        machine.motor.pot_zero_with = 1;
        system_flags.pot_zero_width = 1;
    }
    else
    {
        machine.motor.pot_zero_with = 0;
        system_flags.pot_zero_width = 0;
    }
}

static void task_initializing(void)
{
    control_set_enable_motor(DISABLE);
    set_state_idle();
}

static void task_idle(void)
{
    control_set_enable_motor(DISABLE);
    check_pot_zero();

    if (system_flags.motor_on && system_flags.dms && machine.motor.pot_zero_with)
    {
        set_state_running();
    }
}

static void task_running(void)
{
    control_set_enable_motor(ENABLE);
    control_set_duty_target(machine.motor.duty);

    if (!system_flags.motor_on || !system_flags.dms)
    {
        set_state_idle();
    }
}

static void task_error(void)
{
    LOG_ERROR("error");
    set_state_idle();
}

/*
**  PUBLIC FUNCTIONS
*/
void machine_init(void)
{
    LOG_INFO("initializing machine");
    set_state_initializing();
}

void machine_set_motor_duty(float D)
{
    machine.motor.duty = D;
}

void machine_set_motor_on(FunctionalState motor_on)
{
    machine.motor.motor_on = motor_on;
}

void machine_set_motor_dms(FunctionalState dms)
{
    machine.motor.dms = dms;
}

void machine_set_motor_reverse(FunctionalState reverse)
{
    machine.motor.reverse = reverse;
}

void machine_set_run(void)
{
    machine.run = 1;
}

void machine_run(void)
{

    if (machine.run)
    {
        machine.run = 0;
        can_task_run();
        control_run();
        HAL_GPIO_TogglePin(GPIOC, GPIO_PIN_15);
        switch (machine.state)
        {
        case STATE_INITIALIZING:
            task_initializing();
            break;
        case STATE_IDLE:
            task_idle();
            break;
        case STATE_RUNNING:
            task_running();
            break;
        default:
            LOG_WARN("Unrecognized machine state!");
        case STATE_ERROR:
            task_error();
            break;
        }
    }
}

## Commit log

2020-10-06 Simulation with mosfet logic working
    [4q_truth_table.csv]
2020-10-06 Add the digital embedded controller and more
    - Discrete PWM Controller added: not in use, just for reference.
    - Embedded Controller added, with the code from MCB19
    - Ideal Voltage and Current sensors added for both Input and Output.
    - Signal Conditioning added, with ideal filters and gains.
    - PWM Peripheral added, using SAR topology, containing delay between
    channels, a common clock feeding a sample/hold.
    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
2020-10-06 Add script to test the equation of the PWM controller
2020-10-06 Firmware cleanup and basic setup with the following tests:
    - ADC_CLOCK and MACHINE_CLOCK signals: ok
    - ADC_CLOCK frequency is correct: ???
    - MACHINE_CLOCK frequency is correct: ???
    - ADC reading values and calibrated: ok
    - Filters and gain are working: ok
    - Enable, Regen, Rev, Power signals: ok
    - PWMs signals are being generated: ok
    - motor controller functions are working: ok
2020-10-06 Implement simple 4 quadrant test case using the Pilot Controller
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2020-10-08 Ideal simulation (#10)
    * Simulation with mosfet logic working
    * Add the digital embedded controller and more
    - Pilot Controller added, with the basic controllers being:
    - Power, to set the desired motor output power.
    - Enable, to safely turn on/off.
    - Rev, to select motor direction.
    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
    [4q_truth_table.csv]
2020-10-29 ME0909 modelling data and scripts added
    [F0000CH1.CSV, F0000CH2.CSV, F0002CH1.CSV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]
2020-10-29 Add datasheet and its extracted data
    [Amps.csv, Eff.csv, RPM.csv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]
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2020-10-29 Plots and prints fixed
2021-01-02 Add data extracted from Performance Data using WebPlotDigitizer
    [24V CCW Amps.csv, 24V CCW Eff.csv, 24V CCW RPM.csv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]
2021-03-09 starting Mosfet PCB
    [Switches.kicad_pcb, Switches.sch]
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2021-04-02 placa de controle
    [Controle.kicad_pcb, Controle.sch, canbus_connector.sch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]
2021-04-03 adicionado o TL7726 e modificada a placa
    [Controle.kicad_pcb, Controle.sch, STM32.sch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]
2021-04-04 wip: switches pcb routed
    [Swiches.FCStd, Switches.kicad_pcb, Switches.sch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]
2021-04-05 Driver and MOSFETs protections added, driver calculations done.
    [Switches.sch, Switches3.kicad_pcb]
2021-04-08 wip: PCB updated
    [Switches.kicad_pcb, Switches.sch, Switches1.kicad_pcb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]
2021-04-08 control PCB updated
    [Controle.kicad_pcb, Controle.sch, Powersupply.sch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]
2021-04-09 Updating Switches PCB
    [Switches.kicad_pcb, Switches.sch]
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2021-04-09 Update Controle PCB
    [Controle.kicad_pcb, Controle.sch, Powersupply.sch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]
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2021-04-10 first version of layout
    [Controle.kicad_pcb, Controle.sch, Powersupply.sch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]
2021-04-10 falta acabamento
    [Controle.kicad_pcb, Controle.sch, Powersupply.sch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]
2021-04-11 Controle PCB waiting revision
    [Controle.kicad_pcb, Controle.sch, fan.sch]
2021-04-12 Add capacitor PCB
    [Caps.kicad_pcb, Caps.sch, Caps_first.kicad_pcb]
2021-04-12 PCB updated, not yet finished
    [Switches.kicad_pcb, Switches.sch]
2021-04-12 more vias!
    [Controle.kicad_pcb, canbus_connector.sch]
2021-04-12 Done, not yet checked
    [Switches-B_Cu.gbr, Switches-B_Mask.gbr, Switches-B_Paste.gbr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]
2021-04-12 A lot of clarance issues fixed
    [Caps.kicad_pcb]
2021-04-12 Changed to 4 layers because the need of tg-150 material. Gerbers added.
    [Switches-B_Mask.gbr, Switches-B_Paste.gbr, Switches-B_SilkS.gbr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]
2021-04-12 wip controle holes
    [Switches.kicad_pcb]
2021-04-12 A lot of clarance issues fixed, gerbers added
    [Caps-B_Cu.gbl, Caps-B_Mask.gbs, Caps-Edge_Cuts.gm1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]
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2021-04-12 export files
    [Controle-B_Cu.gbl, Controle-B_Mask.gbs, Controle-B_Paste.gbp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]
2021-04-12 dimensions and holes modified
    [Controle-B_Cu.gbl, Controle-B_Mask.gbs, Controle-B_Paste.gbp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]
2021-04-12 PCB updated with holes
    [Caps.kicad_pcb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]
2021-04-12 Remove smd references and values from silkscreen.
    [Caps-B_Cu.gbl, Caps-B_Mask.gbs, Caps-Edge_Cuts.gm1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]
2021-04-12 Add Kicad 3D stack.
    [PCBs_3D.FCStd]
2021-04-12 dimensions reduced
    [Controle.kicad_pcb]
2021-04-12 controle GERBER
    [Controle-B_Cu.gbl, Controle-B_Mask.gbs, Controle-B_Paste.gbp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]
2021-04-12 wip 3D
    [PCBs_3D.FCStd]
2021-04-12 basic 3D positioning done.
    [PCBs_3D.FCStd]
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2021-04-12 silkscreen and export gerbers
    [Switches-B_Cu.gbl, Switches-B_Mask.gbs, Switches-B_Paste.gbp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]
2021-04-12 small changes (compnents values)
    [Switches.sch, canbus.sch]
2021-04-12 Gerbers re-generated with JCLJCLJLC.. string
    [Caps-B_Cu.gbl, Caps-B_Mask.gbs, Caps-B_SilkS.gbo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]
2021-04-12 Add more holes to better pull the heatsink
    [Switches-B_Cu.gbl, Switches-B_Mask.gbs, Switches-B_Paste.gbp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]
2021-04-12 Remove the solder mask from heatsink region
    [Switches-B_Cu.gbl, Switches-B_Mask.gbs, Switches-B_Paste.gbp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]
2021-04-12 3D updated, copper bars added with holes
    [PCBs_3D.FCStd]
2021-04-12 Gerbers updated
    [Switches-B_Cu.gbl, Switches-B_Mask.gbs, Switches-B_Paste.gbp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]
2021-04-28 Add mechanical files
    [ESC.FCStd, PCBs_3D.FCStd, busbars.FCStd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]
2021-04-28 Updated PCB for fabrication
    [Switches-B_Cu.gbl, Switches-B_Mask.gbs, Switches-B_Paste.gbp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]
2021-04-28 Update from last development cycle
    [24V CCW Amps.csv, 24V CCW Eff.csv, 24V CCW RPM.csv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]
2021-04-28 Update busbar size and reassembly the parts together
    [ESC.FCStd, busbars.FCStd, caps.FCStd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]
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2022-07-19 add an inefficient way to turn off PWM in the initial state and when boat off message is received, this code need to be refactored
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2022-08-03 FIX: add missing break in control state machine
    [control.c]
2022-08-03 CONTROL: fix pwm control action
    [control.c]
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2022-08-05 control: fixed error that ignore control action when control error was negative, due to bad control error calculation
    [control.c]
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2022-08-05 h_bridge: invert duty cycle if channel is in pwm mode 2
    [h_bridge.c]
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2022-08-29 update kicad files to kicad 6
    [Controle.kicad_sch, Powersupply.kicad_sch, STM32.kicad_sch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]
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

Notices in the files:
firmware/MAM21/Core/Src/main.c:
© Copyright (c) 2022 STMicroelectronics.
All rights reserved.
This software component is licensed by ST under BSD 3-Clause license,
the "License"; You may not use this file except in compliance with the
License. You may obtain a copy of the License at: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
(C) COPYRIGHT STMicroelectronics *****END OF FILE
